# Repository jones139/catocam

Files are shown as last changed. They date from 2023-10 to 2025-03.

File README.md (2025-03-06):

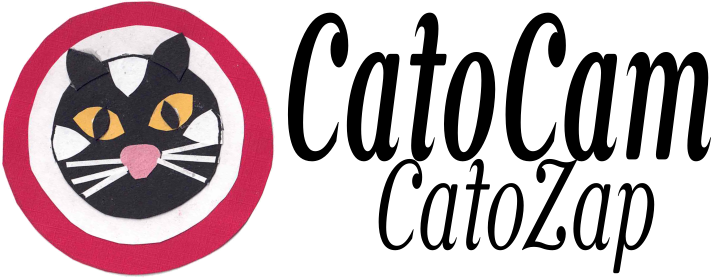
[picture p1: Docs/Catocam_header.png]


CatoCam & CatoZap - monitor a cctv camera to detect cats (CatoCam), and unleash a suitable cat deterrent (CatoZap).

Purpose
=======
The purpose of CatoCam/CatoZap is to deter cats from regarding our garden as their territory humanely.   We do not appreciate what they leave behind!

Project Outline
===============
There are two distinct parts to the project - CatoCam and CatoZap

Catocam monitors the video stream from a [Tp-Link tapo](https://www.tp-link.com/uk/home-networking/cloud-camera/tapo-c510w/) cctv camera by connecting to its local network rtsp stream to grab frames.  
tapo camera picture 

It uses a machine learning object detection model [YoloV8](https://yolov8.com) to determine whether the frame contains an image of a cat or not.

It provides a web interface which can be monitored to see when a cat is detected.

When CatoCam detects that a cat has loitered in the garden for more than a few seconds, it uses CatoZap to encourage the cat to move on.  CatoZap is a simple interface to allow a raspberry Pi to control small solenoid valves to switch water jects on and off when required.  

I might try extending it to use an ultrasonic deterrent as done in this [similar project](https://medium.com/@james.milward/deterring-foxes-and-badgers-with-tensorflow-lite-python-raspberry-pi-ring-cameras-ultrasonic-75b3160faa3c).

CatoCam Structure
=================
  - Connect to the camera rtsp stream using the [framegrab](https://pypi.org/project/framegrab/) library
  - Grab a frame
  - Detect cats in the frame using a custom trained [YoloV8](https://yolov8.com) model (see below).
  - Save annotated frames that contain detected cats, birds or humans to disk for future analysis
  - Provide a simple web interface using the [Flask](https://pypi.org/project/Flask/) framework, which has the following functions:
      - View current image on web browser.
      - Browse through previous images where cats, birds or humans were detected.
      - Provide a simple status JSON object with detection status that can be monitored by CatoZap
  - It is configured using a simple JSON config.json file that specifies the camera parameters to access the video stream, and the object detection model to be used (see the example [config.json template](./config_template.json))
  - If it detects a cat in two frames within 15 seconds of each other, it treats this as a 'cat event', which lasts until no cat is detected for 30 seconds.
  - During a cat event, it calls on CatoZap to fire its water jets to encourage the cat to move along.
  - When the cat event finishes, it concatenates all of the image frames that have been collected during the event into a single movie file and saves it to disk.

  Catocam is running on a Raspberry Pi 4B, 2GB memory and achieving 0.6 frames per second.  I am hoping to improve this by using a quantized version of the yolov8n model.

  An example output is shown below:
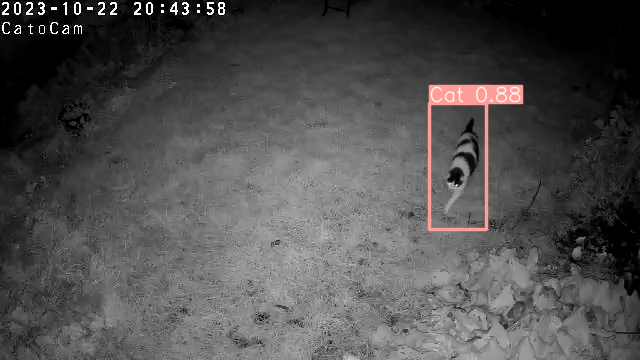
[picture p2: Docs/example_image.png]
  

Training the YoloV8 Model
=========================
If found that pre-trained object detection models were giving poor performance on my cctv images, probably for two reasons:
  1. The camera angle is looking down on the  scene, which is not the case for most image libraries.
  2. The images are often taken under infrared illumination so are grey scale not colour

For this reason I modified the YoloV8 model by training it on my own models.   This required the following:
  - Set up the camera and have it monitor the garden, recording video clips when motion was detected.
  - View the video clips to identify which ones contain cats, and download them (You actually have to download the videos onto a phone as there is no computer interfae to the Tapo camera, only and Android App.  So the process was to view the video on my phone, download it onto my phone, and upload it to Google Photos.  I could then download it onto my computer using the Google Photos web site).
    
  - Use the [RoboFlow](https://roboflow.com) web site to create an annotated dataset by using its capabilities to:
      - split the video clips into frames
      - view each frame
      - let me draw a bounding box around the interesting objects (cats, birds or humans), and label them as such.
      - Add the images to a dataset, along with augmentation of the objects in the bounding boxes.
      - Publish the [dataset](https://universe.roboflow.com/graham-jones-yynmh/catocam) <a href="https://universe.roboflow.com/graham-jones-yynmh/catocam">
    
</a>
  - The annotation was made less tedious by first doing a few (well a hundred or so) frames manually, then using RoboFlow's training functionality (you get three goes at training a model with a free account), to create an object detection model.   This object detection model can then be used to help you annotate other images by suggesting what the bounding box and object is, so you only have to correct it when it has something wrong.

  - Export the Roboflow dataset in YoloV8 format, and extract it to ~/yolo/datasets/CatoCam.<version number>
  - Create a python virtual environment for catocam: python -m venv /home/graham/pyEnvs/catocam
  - Activate catocam environment with source ~/pyEnvs/catocam/bin/activate
  - Change directory to this catocam source directory.
  - Install dependencies with pip install -r requirements.txt
  - Use the simple [trainYolo.py](./yolo/trainYolo.py) script to train the model using our new dataset.
      - This creates a new set of weights for the yolo model, which we saved as [catFinderV8_yoloWeights.pt](./catFinderV8_yoloWeights.pt) for use by CatoCam.

### Results
The results were surprisingly good - we detected cats very well.   But, it detected pigeons as cats too, and I might not want to shoot the pigeons, so I introduced an extra category 'bird'.  I also found it was detecting people as cats sometimes, so I added a set of images of people and an extra category 'human'.   Having done that we seem to be detecting cats, birds and humans quite well.

Now the camera I am using will track motion to keep the moving object in the field of view.   This does mean that the background can change quite a bit and I found that if it saw the edge of a wall, or a barrel shaped compost bin it was marking this as a human.   This is not too big a deal because I won't be shooting humans, but I'd rather it got it right.  So I added more images of other things it might see in the garden and marked them as null (not a cat, bird or human).   This is now working pretty well, but I do get the occasional 'human' detection for a close up of a cobweb under the IR floodlight, so I'll need to add some cobweb images in too.

I also have the idea of using this with several cameras in different positions around the garden, so I have installed on next to the drive.   Initial results suggest it still detects humans ok, but it sees other shapes like windows and the gate posts as humans - I think it has larned that tall, narrow things are human....  So I have collected a lot more negative images and are currently training those into the model so we can see if it can detect cats in a different setting to the training images - ie to see how generic the model is.   I might see if [James Milward](https://medium.com/@james.milward/deterring-foxes-and-badgers-with-tensorflow-lite-python-raspberry-pi-ring-cameras-ultrasonic-75b3160faa3c) is interested in comparing results on each others datasets...

CatoZap
=======
The hardware side of CatoZap utilises 12V solenoid valves connected to the water main using 1/4" plastic tubing.   An interface board is used to switch the 12V required for the valves using the GPIO output from the Raspberry Pi that is running CatoCam.
I have used the these valves <a href="https://www.amazon.co.uk/dp/B08KS5MMYK?ref=ppx_yo2ov_dt_b_product_details&th=1">12V Solenoid Valve (1/4" tube) </a> with this tubing <a href="https://www.amazon.co.uk/dp/B07H2VGR71?psc=1&ref=ppx_yo2ov_dt_b_product_details">1/4" plastic tube </a>

The interface for the Raspberry Pi is currently a three channel transistor based driver for the solenoids, using the circuit shown [here](./catozap/Electrical/catozap_schematic.pdf) 

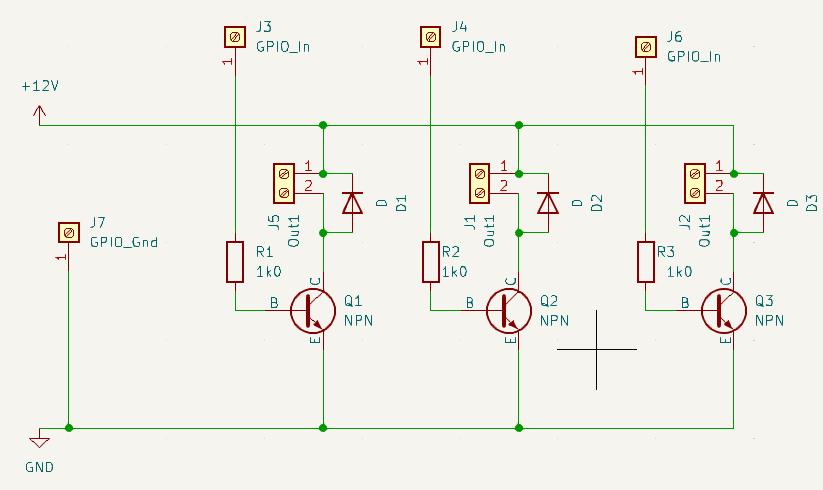
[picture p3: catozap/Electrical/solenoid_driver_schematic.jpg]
.   

It connects to the ground and GPIO7, GPIO27 and GPIO22 outputs (because they are all next to each other and next to a ground pin on the Raspberry Pi header.
The prototype board which is assembled on stripboard is shown below:  
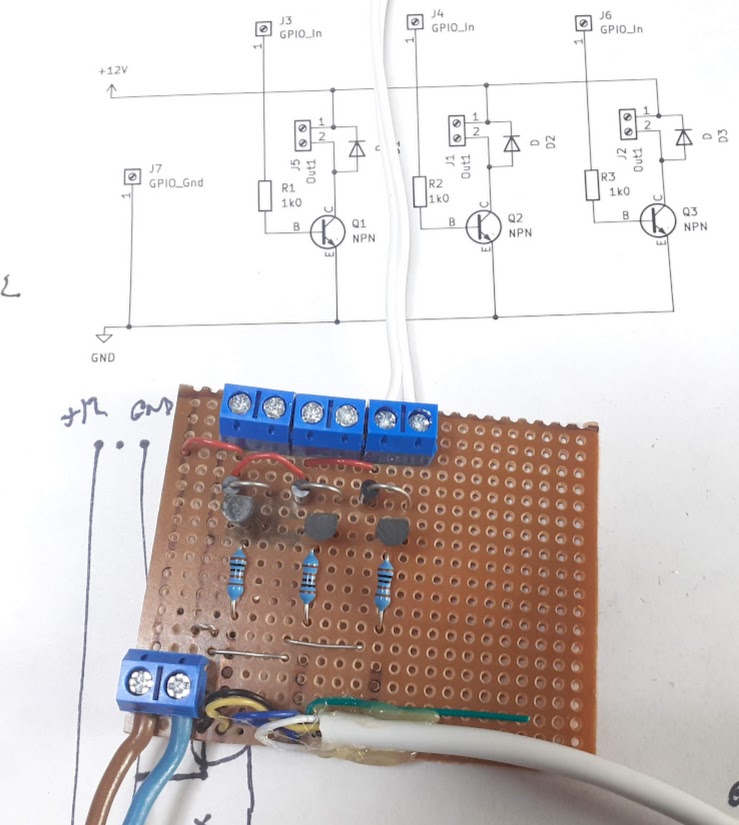
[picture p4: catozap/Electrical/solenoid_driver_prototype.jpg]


Contact
=======
If anyone tries to use this and needs any help, please contact graham@openseizuredetector.org.uk, or raise an issue on this site.

Licence
=======
All code is GPL V3 - see [LICENSE](./LICENSE).

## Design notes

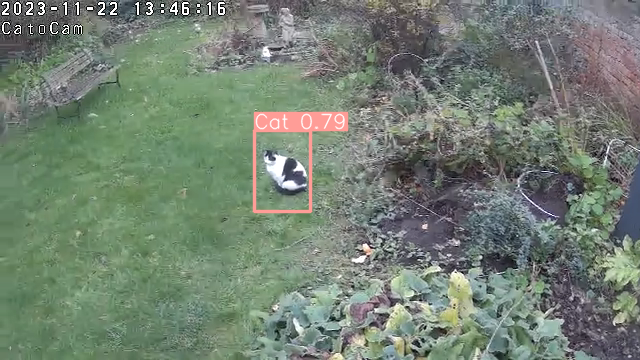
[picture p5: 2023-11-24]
Docs/example_image2.png

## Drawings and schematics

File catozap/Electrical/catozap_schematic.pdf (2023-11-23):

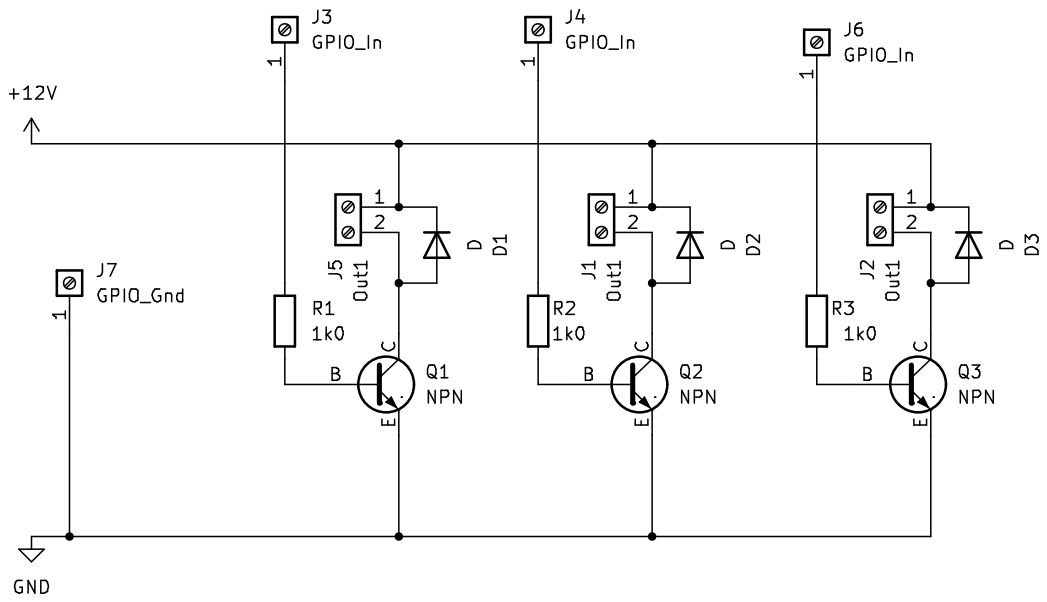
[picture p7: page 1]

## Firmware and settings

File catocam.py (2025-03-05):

#!/usr/bin/env python
import importlib
import sys
import os
import time
import datetime
import cv2
import threading

import argparse
import json
import framegrab

import catSvr

import flask
import datetime

import paho.mqtt.client as mqtt

import catozap

class CatoCam():
    def __init__(self, configObj, debug=None):
        self.debug = False
        if debug is not None:
            self.debug = debug
        else:
            if "debug" in configObj:
                self.debug = configObj['debug']
        print("CatoCam.__init__() - debug=%s" % self.debug)

        self.mModels = []
        self.configObj = configObj

        self.outDir = configObj['outDir']
        if not os.path.exists(self.outDir):
            os.makedirs(self.outDir)

        # Load the cat detection model(s)
        self.loadModels()

        self.foundCat = False
        self.lastFoundCat = False
        self.foundSomething = False
        self.currImg = None
        self.lastPositiveImg = None
        self.imgTime = time.time()
        self.lastPositiveImgTime = None
        self.lastCatImgTime = None
        self.catEventActive = False
        self.catEventStartTime = None
        self.fps = 0
        self.framesLst = []

        # Start the catozap water zapper service.
        if (configObj['catoZap']['enabled']):
            print("Starting CatoZap")
            self.cz = catozap.CatoZap(configObj['catoZap'])
            self.cz.start()
        else:
            print("CatoZap disabled, not sarting")
            self.cz = None

        if (configObj['catoZapMqtt']['enabled']):
            print("Using CatoZapMqtt")
            self.useMqtt = True
            self.mqttClient = mqtt.Client(mqtt.CallbackAPIVersion.VERSION1,
                                          "catocam")
            self.mqttClient.on_publish = self.on_mqtt_publish
            self.mqttClient.connect(configObj['catoZapMqtt']['brokerIp'], 1883)
            # start a new thread
            self.mqttClient.loop_start()
            self.doMqttZap()
            self.reportCatMqtt(self.foundCat)

        else:
            self.useMqtt = False

    def on_mqtt_publish(self, client, userdata, mod):
        print("sent mqtt message")

    def doMqttZap(self):
        print("doMqttZap")
        msg = "ALL"
        info = self.mqttClient.publish(
            topic=self.configObj['catoZapMqtt']['zapTopic'],
            payload=msg.encode('utf-8'),
            qos=0,
        )

    def reportCatMqtt(self, catStatus = False):
        print("reportCatMqtt")
        msg = "%d" % catStatus
        info = self.mqttClient.publish(
            topic=self.configObj['catoZapMqtt']['catTopic'],
            payload=msg.encode('utf-8'),
            qos=0,
        )

           
    def loadModels(self):
        if not "models" in self.configObj:
            print("CatoCam.loadModels() - ERROR - configObj does not contain a 'models' element.")
            raise
        for modelCfg in self.configObj['models']:
            moduleId = modelCfg['class'].split('.')[0]
            classId = modelCfg['class'].split('.')[1]
            print("Importing Module %s" % moduleId)
            module = importlib.import_module(moduleId)
            self.mModels.append((
                modelCfg['name'],
                eval("module.%s(modelCfg['settings'], self.debug)" % (classId))))
        
        for m in self.mModels:
            print("Model %s" % m[0])


    def getOutSubDir(self):
        todaysDate = datetime.datetime.now()
        outFolder = todaysDate.strftime("%Y-%m-%d")
        outSubDir = os.path.join(self.outDir, outFolder)
        if not os.path.exists(outSubDir):
            os.makedirs(outSubDir, exist_ok=True)
        return(outSubDir)

    def recordCat(self, retObj, img):
        todaysDate = datetime.datetime.now()
        outSubDir = self.getOutSubDir()
        imgFname = "catocam-%s-%s.png" % (retObj['predictions'][0]['class'], todaysDate.strftime("%H_%M_%S"))
        logFname = "catocam.log"
        cv2.imwrite(os.path.join(outSubDir,imgFname), img)

        fp = open(os.path.join(outSubDir, logFname),"a")
        timeStr = todaysDate.strftime("%Y/%m/%d %H:%M:%S")
        pred =retObj['predictions'][0]
        print("\n%s: class = %s (%.2f%%) " % (timeStr, pred['class'], pred['confidence']))
        if pred['confidence'] > 0.5: #self.mModels[0][1].thresholds[pred['class']]:
            fp.write("\"%s\", %s, %.f%%, %s\n" % (timeStr, pred['class'], pred['confidence']*100., imgFname))
        fp.close()

    def saveCatEventVideo(self):
        todaysDate = datetime.datetime.now()
        outSubDir = self.getOutSubDir()
        vidFname = "catocam-%s.mp4" % (todaysDate.strftime("%Y_%m_%d_%H_%M_%S"))
        print("saveCatEventVideo() - saving to file %s in folder %s" % (vidFname, outSubDir))
        print("saveCatEventVideo() - saving %d frames of size (%d, %d)" % (len(self.framesLst), self.currImg.shape[1], self.currImg.shape[0]))
        out = cv2.VideoWriter(os.path.join(outSubDir, vidFname), cv2.VideoWriter_fourcc(*'mp4v'), 1, (self.currImg.shape[1], self.currImg.shape[0]))
        for frame in self.framesLst:
            out.write(frame) # frame is a numpy.ndarray with shape (1280, 720, 3)
        out.release()
        print("saveCatEventVideo() - finished!")


    
    def getOutputFoldersLst(self):
        ''' Return a list of the sub-folders in the self.outDir folder.'''

        dirLst = [ item for item in os.listdir(self.outDir) if os.path.isdir(os.path.join(self.outDir, item)) ]
        dirLstSorted = sorted(dirLst, key=lambda item: os.path.getctime(os.path.join(self.outDir, item)))

        # from https://www.tutorialspoint.com/How-do-you-get-a-directory-listing-sorted-by-creation-date-in-Python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.,listing%20based%20on%20creation%20date.
        #def sorted_directory_listing_by_creation_time_with_os_listdir(directory):
        #    def get_creation_time(item):
        #        item_path = os.path.join(directory, item)
        #        return os.path.getctime(item_path)

        #    items = os.listdir(directory)
        #    sorted_items = sorted(items, key=get_creation_time)
        #    return sorted_items

        return dirLstSorted
    
    def getSavedImgLst(self, dirName):
        ''' Return a list of the image file names in folder self.outDir/dirname'''
        imgLst = [ item for item in os.listdir(os.path.join(self.outDir, dirName)) 
                  if item.lower().endswith(('.png', '.jpg', '.jpeg')) ]
        imgLstSorted = sorted(imgLst, key=lambda item: os.path.getctime(os.path.join(self.outDir, dirName, item)))

        return imgLstSorted

    def getSavedVideoLst(self, dirName):
        ''' Return a list of the video file names in folder self.outDir/dirname'''
        imgLst = [ item for item in os.listdir(os.path.join(self.outDir, dirName)) 
                  if item.lower().endswith(('.mp4')) ]
        imgLstSorted = sorted(imgLst, key=lambda item: os.path.getctime(os.path.join(self.outDir, dirName, item)))

        return imgLstSorted


    def getHistoryImgByIndex(self, dirName, idx):
        imgLst = self.getSavedImgLst(dirName)
        imgFname = imgLst[idx]
        imgPath = os.path.join(self.outDir, dirName, imgFname)
        print("getHistoricalImg() - file path=%s" % imgPath)
        img = cv2.imread(imgPath)
        return img


    def getHistoryImg(self, dirName, imgFname):
        imgPath = os.path.join(self.outDir, dirName, imgFname)
        print("getHistoricalImg() - file path=%s" % imgPath)
        img = cv2.imread(imgPath)
        return img

    def analyseImage(self, img):
        '''
        Analyses image img using the first model in self.mModels
        sets instance variables imgTime, foundCat, currImg, lastPositiveImg, lastPositiveImgTime and
        foundSomething.
        Returns true if a cat is found or else false.'''
        modelName, modelClass = self.mModels[0]
        self.imgTime = time.time()
        self.foundCat, retObj = modelClass.findCat(img)
        
        #print(modelName, foundCat, retObj)
        foundSomething = False
        for pred in retObj['predictions']:
            if pred['confidence']>0.5:
                foundSomething = True

        if foundSomething:
            # create an annotated image showing the bounding box of the found objects.
            annotatedImg = modelClass.getAnnotatedImage(img)
            # Write to the log file, and save teh annotated image.
            self.recordCat(retObj, annotatedImg)
            self.currImg = annotatedImg
            self.lastPositiveImg = annotatedImg
            self.lastPositiveImgTime = self.imgTime
            self.framesLst.append(annotatedImg)
            self.foundSomething = True
        else:
            self.currImg = img
            self.foundSomething = False
            self.framesLst.append(img)


        if (self.foundCat != self.lastFoundCat):
            if (self.useMqtt):
                self.reportCatMqtt(self.foundCat)
            self.lastFoundCat = self.foundCat
            
        # Check if we are in a cat event - a cat event is started by two cat detections within 15 seconds.
        # It ends 30 seconds after the last cat detection.
        if self.foundCat:
            if (not self.catEventActive):
                if (self.lastCatImgTime is None) or (self.imgTime - self.lastCatImgTime) > 15:
                    print("we have two cat detections within 15 seconds, so we are in a cat event...")
                    self.catEventActive = True
                    self.catEventStartTime = self.lastCatImgTime

            self.lastCatImgTime = self.imgTime
        else:
            if (self.catEventActive):
                if (self.imgTime - self.lastCatImgTime) > 5: # was 30 FIXME
                    print("End of Cat Event")
                    self.catEventActive = False
                    self.catEventStartTime = None
                    self.saveCatEventVideo()

        if not self.catEventActive:
            if len(self.framesLst) > 10:
                self.framesLst = self.framesLst[-10:]
                #print("Truncating framesLst - len=%d" % len(self.framesLst))

        return self.foundSomething

    def testFile(self, testFname, fps = 1):
        print("CatoCam.testFile() - testFname=%s" % testFname)
        cap = cv2.VideoCapture(testFname)
        fileFps = cap.get(cv2.CAP_PROP_FPS)
        FRAME_BATCH_SIZE = fileFps / fps
        success = True
        nFrames = 0
        batchStartTime = time.time()
        while success:
            success, img = cap.read()
            nFrames += 1
            tdiff = time.time() - batchStartTime
            if (success):
                if tdiff > 1.0:
                    self.fps = nFrames / tdiff
                    print("%d frames in %.1f sec - %.1f fps" % (nFrames, tdiff, self.fps))
                    self.analyseImage(img)
                    batchStartTime = time.time()
                    nFrames = 0
        print("End of file?")
        if (self.catEventActive):
            self.saveCatEventVideo()
        print("CatoCam.testFile finished!")


    def getFrames(self, testFname=None):
        if testFname is not None:
            self.testFile(testFname)
            return
        
        camArr = []
        for cam in self.configObj["cameras"]:
            print("getFrames() adding camera")
            # Tp-Link Tapo camera RTSP stream - stream1 is high quality, stream2 low quality.
            print("Adding Camera: ", cam)
            grabber = framegrab.FrameGrabber.create_grabber(cam)
            camArr.append(grabber)

        FRAME_RATE_REQ = self.configObj['maxFps']
        FRAME_BATCH_SIZE = int(FRAME_RATE_REQ)
        FAIL_RESTART_COUNT = 10
        nFrames = 0
        batchStartTime = time.time()
        iterDurationReq = 1.0/FRAME_RATE_REQ

        print("Looking for Cats......")
        failCount = 0
        while(1):
            iterStartTime = time.time()
            img = grabber.grab()
            if (img is not None):
                #cv2.imshow("frame", img)
                self.analyseImage(img)
                failCount = 0
            else:
                print("CatoCam.getFrames(): WARNING: Failed to retrieve image from camera")
                failCount += 1
                if (failCount >= FAIL_RESTART_COUNT):
                    print("CatoCam.getFrames(): Restarting frame Grabber")
                    grabber = framegrab.FrameGrabber.create_grabber(cam)
                    failCount = 0

            if (self.catEventActive):
                if (self.cz is not None):
                    print("CatoCam.getFrames() - Cat Event Active - Firing!")
                    self.cz.fire()
                if (self.useMqtt):
                    self.doMqttZap()

            nFrames += 1
            tdiff = time.time() - batchStartTime
            if tdiff > 1.0:
                self.fps = nFrames / tdiff
                sys.stdout.write("%d frames in %.1f sec - %.1f fps\r" % (nFrames, tdiff, self.fps))
                sys.stdout.flush()
                batchStartTime = time.time()
                nFrames = 0
            if cv2.waitKey(20) & 0xFF == ord('q'):
                break

            # Reduce frame rate to desired  rate.
            tnow = time.time()
            iterDuration = iterStartTime - tnow
            if (iterDuration < iterDurationReq):
                time.sleep(iterDurationReq - iterDuration)
                pass
            else:
                print("Not Sleeping - too slow!")

        for cam in camArr:
            cam.release()
        #camArr[0].release()
        #cv2.destroyAllWindows()
        print("Finished")




if __name__ == "__main__":
    print("catocam.main()")
    parser = argparse.ArgumentParser(description='Detect Cats in Video Streams')
    parser.add_argument('--config', default="config.json",
                        help='name of json configuration file')
    parser.add_argument('--test', default=None,
                        help='run the system on a test video file rather than live data')
    #parser.add_argument('--index', action="store_true",
    #                    help='Re-build index, not all summaries')
    parser.add_argument('--debug', action="store_true",
                        help='Write debugging information to screen')
    
    argsNamespace = parser.parse_args()
    args = vars(argsNamespace)
    print(args)

    infile = open(args['config'])
    configObj = json.load(infile)
    print(configObj)
    cc = CatoCam(configObj, debug=args['debug'])
    print("Starting web server")
    cs = catSvr.CatSvr(cc)
    print("Creating Web Server Thread")
    wsThread = threading.Thread(target=cs.run, args=("catSvr",))
    print("Starting Web Server Thread")
    wsThread.start()
    print("starting CatoCam analyser")
    if args['test'] is not None:
        testFname = args['test']
        print("Testing using file %s" % testFname)
        cc.getFrames(testFname=testFname)
    else:
        print("Monitoring Live Camera Streams")
        cc.getFrames(testFname=None)

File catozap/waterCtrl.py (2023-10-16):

#!/usr/bin/python3

# Greenhouse water controller interface
# Assumes water control valve is actuated by GPIO pin
# cfg['waterControlPin']

import os
import time
import datetime
import threading
import logging
import RPi.GPIO as GPIO
import simple_pid
import dbConn
import monitorDaemon

class _waterCtrlThread(threading.Thread):
    def __init__(self, cfg, debug = False):
        print("_waterCtrlThread.__init__()")
        self.cfg = cfg
        self.logger = logging.getLogger(self.cfg['logName'])
        self.waterControlPin = cfg['waterControlPin']
        threading.Thread.__init__(self)
        self.dbPath = os.path.join(cfg['dataFolder'],cfg['dbFname'])

        # Initialise settings from database, or config file if DB values not set
        self.db = dbConn.DbConn(self.dbPath)
        dbSetpoint, dbKp, dbKi, dbKd, dbCycleSecs, dbControlVal, dbOnSecs, dbOpMode, dbLightThresh = self.db.getWaterControlVals()
        self.db.close()
        if (dbOpMode is None):
            self.opMode = cfg['opMode']
        else:
            self.opMode = dbOpMode
        if (dbOnSecs is None):
            self.onSecs = cfg['waterOnSecs']
        else:
            self.onSecs = dbOnSecs
        if (dbSetpoint is None):
            self.setPoint = cfg['setPoint']
        else:
            self.setPoint = dbSetpoint
        if (dbCycleSecs is None):
            self.cycleSecs = cfg['waterCycleSecs']
        else:
            self.cycleSecs = dbCycleSecs
        if (dbKp is None):
            self.Kp = cfg['Kp']
        else:
            self.Kp = dbKp
        if (dbKi is None):
            self.Ki = cfg['Ki']
        else:
            self.Ki = dbKi
        if (dbKd is None):
            self.Kd = cfg['Kd']
        else:
            self.Kd = dbKd
        if (dbLightThresh is None):
            self.lightThresh = cfg['lightThresh']
        else:
            self.lightThresh = dbLightThresh
        self.timeOnLimit = cfg['timeOnLimit']
            
        self.logger.info("_waterCtrlThread.__init__(): cycleSecs=%f, setpoint=%f" % (self.cycleSecs, self.setPoint))
        self.logger.info("_waterCtrlThread.__init__(): opMode=%s, (Kp,Ki,Kd)=(%f,%f,%f), lightThresh=%f" % (self.opMode, self.Kp, self.Ki, self.Kd, self.lightThresh))

        self.DEBUG = debug
        self.runThread = True
        self.curTime = datetime.datetime.now()
        self.waterStatus = 0
        self.soilCond = -1
        self.soilRes = -1
        self.controlVal = -1

        GPIO.setmode(GPIO.BCM)
        GPIO.setup([self.waterControlPin], GPIO.OUT)
        
    def run(self):
        """
        The main loop of the thread  repeatedly checks to see if it is time
        to switch the water on or off.
        """
        self.logger.info("waterCtrlThread.run()")
        # re-open db for this thread.
        self.db = dbConn.DbConn(self.dbPath)

        self.pid = simple_pid.PID(self.Kp, self.Ki, self.Kd,
                                  setpoint=self.setPoint,
                                  sample_time=None,
                                  output_limits=(0,self.timeOnLimit))
        
        while self.runThread:
            # Start cycle
            self.cycleStartTime = datetime.datetime.now()
            self.db = dbConn.DbConn(self.dbPath)
            data_date, temp1, temp2, temp3, rh, light, soil, soil1, soil2, soil3 = self.db.getLatestMonitorData()
            self.db.close()
            condVals = [soil, soil1, soil2, soil3]
            coldVals = condVals.sort()
            condMedian = (condVals[1]+condVals[2])/2.0
            self.soilCond = condMedian

            if (light>self.lightThresh):
                self.controlVal = self.pid(self.soilCond)
                self.logger.debug("self.soilCond=%.1f, soilVals=(%.1f,%.1f,%.1f,%.1f)" % (self.soilCond, soil, soil1, soil2, soil3))
                # Set the cycle watering on time based on the operating mode
                if (self.opMode=="moist"):
                    self.onSecs = self.controlVal
                    self.logger.info("Cycle_Start: soilCond=%.1f, setPoint=%.1f, controlVal=%.1f" %
                      (self.soilCond, self.setPoint, self.controlVal))
                elif (self.opMode=="time"):
                    self.logger.info("Cycle_Start: onSecs="+str(self.onSecs))
                elif (self.opMode=="off"):
                    self.onSecs = 0
                else:
                    self.logger.error("Unrecognised operating mode '%s'"
                                      % self.opMode)
                    self.onSecs = 0

                # Apply some water
                if (self.onSecs>0):
                    self.waterForTime(self.onSecs)
                else:
                    self.logger.info("onSecs <= 0 secs - not watering")
                    self.writeWaterData()
            else:
                self.logger.info("Low light level so not applying water")
                self.onSecs = 0
                self.controlVal = 0
                self.writeWaterData()

            # Wait for end of cycle
            dt = datetime.datetime.now()
            while (dt - self.cycleStartTime).total_seconds() < self.cycleSecs:
                time.sleep(0.1)
                dt = datetime.datetime.now()
            self.logger.info("end of Cycle")
            if (self.DEBUG): print("_waterCtrlThread.run(): end of Cycle")
        self.logger.info("waterCtrlThread.run() - Exiting")
        self.waterOff()

    def stop(self):
        """ Stop the background thread"""
        self.logger.info("Stopping thread")
        self.runThread = False

    def writeWaterData(self):
        self.db = dbConn.DbConn(self.dbPath)
        dt = datetime.datetime.now()
        self.db.writeWaterData(dt, self.waterStatus,
                               self.onSecs,
                               self.cycleSecs,
                               self.controlVal,
                               self.setPoint,
                               self.Kp,
                               self.Ki,
                               self.Kd,
                               self.opMode,
                               self.lightThresh);
        self.db.close()

    def waterForTime(self, onSecs):
        self.writeWaterData()
        self.waterOn()
        self.waterOnTime = datetime.datetime.now()
        self.writeWaterData()
        self.logger.info("waterOn")
        # Wait for time to switch water off.
        dt = datetime.datetime.now()
        while (dt - self.waterOnTime).total_seconds() < onSecs:
            time.sleep(0.1)
            dt = datetime.datetime.now()
        self.writeWaterData()
        self.waterOff()
        self.writeWaterData()
        self.logger.info("waterOff")

        
    def waterOn(self):
        self.logger.info("waterOn()")
        if (self.DEBUG): print("_waterCtrlThread.waterOn()")
        GPIO.output(self.waterControlPin, GPIO.HIGH)
        self.waterStatus=1
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

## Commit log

2023-10-12 Fixed using hosted roboflow model, and removed delays from loop to try to increase frame rate.
    [catFinderRoboflow.py, catocam.py]
2023-10-13 converted to use framegrab library as it seems to be more stable than my diy opencv implementation.
2023-10-13 Fixed crash if null image is returned from framegrabber.
    [catFinder.py, catocam.py]
2023-10-14 Added helpful error to remind user to start local inference server if necessary
    [catFinderRoboflow.py]
2023-10-16 Added first start at a 'catozap' server to control the water jets - not working yet....
    [WebControlClass.py, bottle.py, catozapSvr.py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]
2023-10-20 Added Yolo version of catfinder model, which we should be able to shrink onto a Raspberry Pi.
2023-10-20 Added tflite version - not working yet
    [catFinderTfLite.py, catocam.py]
2023-10-21 Started a MediaPipe based catFinder (not working), changed back to using 50% confidence rather than user specified confidence thresholds.
    [catFinder.py, catFinderMediaPipe.py, catocam.py]
2023-10-22 Web server working to display current and last positive image.
2023-10-23 Fixed crash on /status related to raspi cpu temperature
    [catSvr.py]
2023-10-23 Formatted date on web page correctly
    [catSvr.py, catocam.py]
2023-10-23 Added fps and cpu temperature to server web pages
2023-10-25 Added prev and next buttons to history web page to make cycling through images easier
2023-10-25 Fixed some crashes with new prev/next functionality - added V8 of yolo model
    [catSvr.py]
2023-11-13 Updates so it works as a systemctl service - added explicit file paths - should really fix this to work relative to the script directory?
    [catSvr.py, catocam.py]
2023-11-23 Added first go at catozap schematic
    [catozap.kicad_pcb, catozap.kicad_sch]
2023-11-23 Changed catozap to common emitter configuration
    [catozap.kicad_sch]
2023-11-23 Added catozap.py to use in a separate thread on the same machine as catocam
2023-11-25 Fixed issue with catozap not actually firing even though it said it was.
    [catFinder.py, catocam.py, catozap.py]
2024-04-20 Update to elecrical schematic
    [catozap.kicad_pcb, catozap.kicad_sch]
